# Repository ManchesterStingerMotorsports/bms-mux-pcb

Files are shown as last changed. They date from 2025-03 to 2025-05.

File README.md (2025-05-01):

# BMS MUX PCB

Initially the pcb scope was only for multiplexing 16 temperature sensor signals to 8, but the scope grew bigger and other stuffs were added.

Designed in Kicad V8

## V1 3D Render
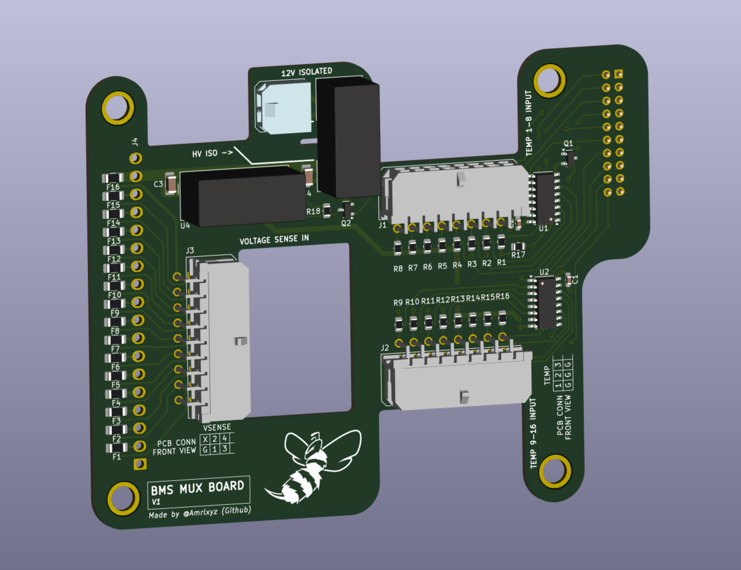
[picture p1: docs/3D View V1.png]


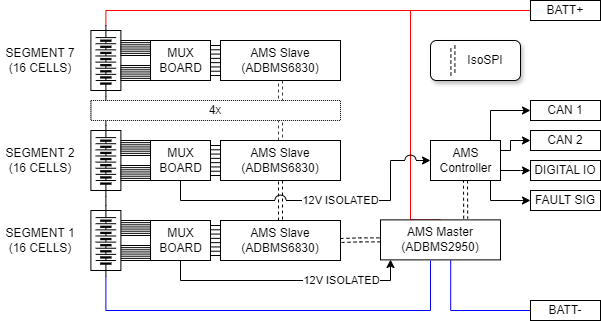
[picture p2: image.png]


### [Schematic](<docs/Schematic V1.pdf>)

### [Layout](<docs/PCB Layout V1.pdf>)

### [Copper Layers](<docs/PCB Copper Layers V1.pdf>)

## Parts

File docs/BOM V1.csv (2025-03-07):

Reference | Value | Datasheet | Footprint | Qty | DNP | Manufacturer Part Number
C1,C2 | 100n | ~ | Capacitor_SMD:C_0603_1608Metric_Pad1.08x0.95mm_HandSolder | 2 |  | CL10B104KB85PND
C3,C4 | 2.2u | ~ | Capacitor_SMD:C_1206_3216Metric_Pad1.33x1.80mm_HandSolder | 2 |  | 885382208016
F1,F2,F3,F4,F5,F6,F7,F8,F9,F10,F11,F12,F13,F14,F15,F16 | Fuse | ~ | Fuse:Fuse_1206_3216Metric_Pad1.42x1.75mm_HandSolder | 16 |  | 0466.250NR
J1,J2 | Conn_02x08_Counter_Clockwise | ~ | BMS-Mux-footprints:Molex_Micro-Fit_3.0_43045-1600_2x08_P3.00mm_Horizontal | 2 |  | 43045-1600
J3 | Conn_02x09_Top_Bottom | ~ | BMS-Mux-footprints:Molex_Micro-Fit_3.0_43045-1800_2x09_P3.00mm_Horizontal | 1 |  | 43045-1800
J4 | Conn_01x18 | ~ | Connector_Wago:Wago_734-148_1x18_P3.50mm_Vertical | 1 |  | 1945151 (x2)
J5 | Conn_01x02 | ~ | BMS-Mux-footprints:Molex_Micro-Fit_3.0_43650-0200_1x02_P3.00mm_Horizontal | 1 |  | 43650-0200
J6 | Conn_02x10_Odd_Even | ~ | Connector_PinHeader_2.54mm:PinHeader_2x10_P2.54mm_Vertical | 1 |  | PH2-20-UA
Q1,Q2 | BSS123 | http://www.diodes.com/assets/Datasheets/ds30366.pdf | Package_TO_SOT_SMD:SOT-23 | 2 |  | BSS123L
R1,R2,R3,R4,R5,R6,R7,R8,R9,R10,R11,R12,R13,R14,R15,R16 | 680R | ~ | Resistor_SMD:R_0805_2012Metric | 16 |  | ERA-6AEB681V
R17,R18 | 16k | ~ | Resistor_SMD:R_0805_2012Metric | 2 |  | ERA-6AEB163V
U1,U2 | 74CBTLV3257 | http://www.ti.com/lit/ds/symlink/sn74cbtlv3257.pdf | Package_SO:SOIC-16_3.9x9.9mm_P1.27mm | 2 |  | SN74LV4053ADR
U3 | TEC2-4812WI | https://www.tracopower.com/products/tec2wi.pdf | Converter_DCDC:Converter_DCDC_TRACO_TMR-xxxx_THT | 1 |  | TEC2-4812WI
U4 | TEC2-4810WI | https://www.tracopower.com/products/tec2wi.pdf | Converter_DCDC:Converter_DCDC_TRACO_TMR-xxxx_THT | 1 |  | TEC2-4810WI

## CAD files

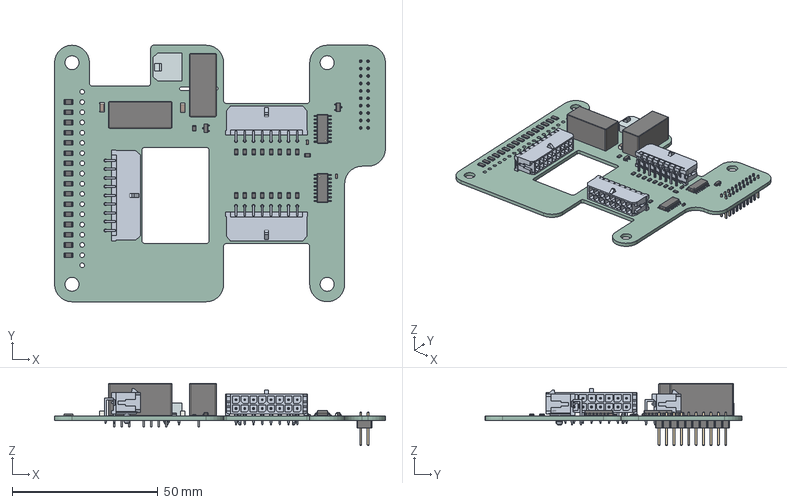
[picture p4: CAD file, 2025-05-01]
docs/BMS-Mux-PCB.step
113.5 x 88.0 x 21.3 mm
R_0805_2012Metric x 18
C_1206_3216Metric x 2
Fuse_1206_3216Metric x 16
436500200wbm000_01
Converter_DCDC_TRACO_TMR_xxxx_THT x 2
SOT_23 x 2
SOIC_16_39x99mm_P127mm x 2
C_0603_1608Metric x 2
PinHeader_2x10_P254mm_Vertical
BMS-Mux-PCB_PCB

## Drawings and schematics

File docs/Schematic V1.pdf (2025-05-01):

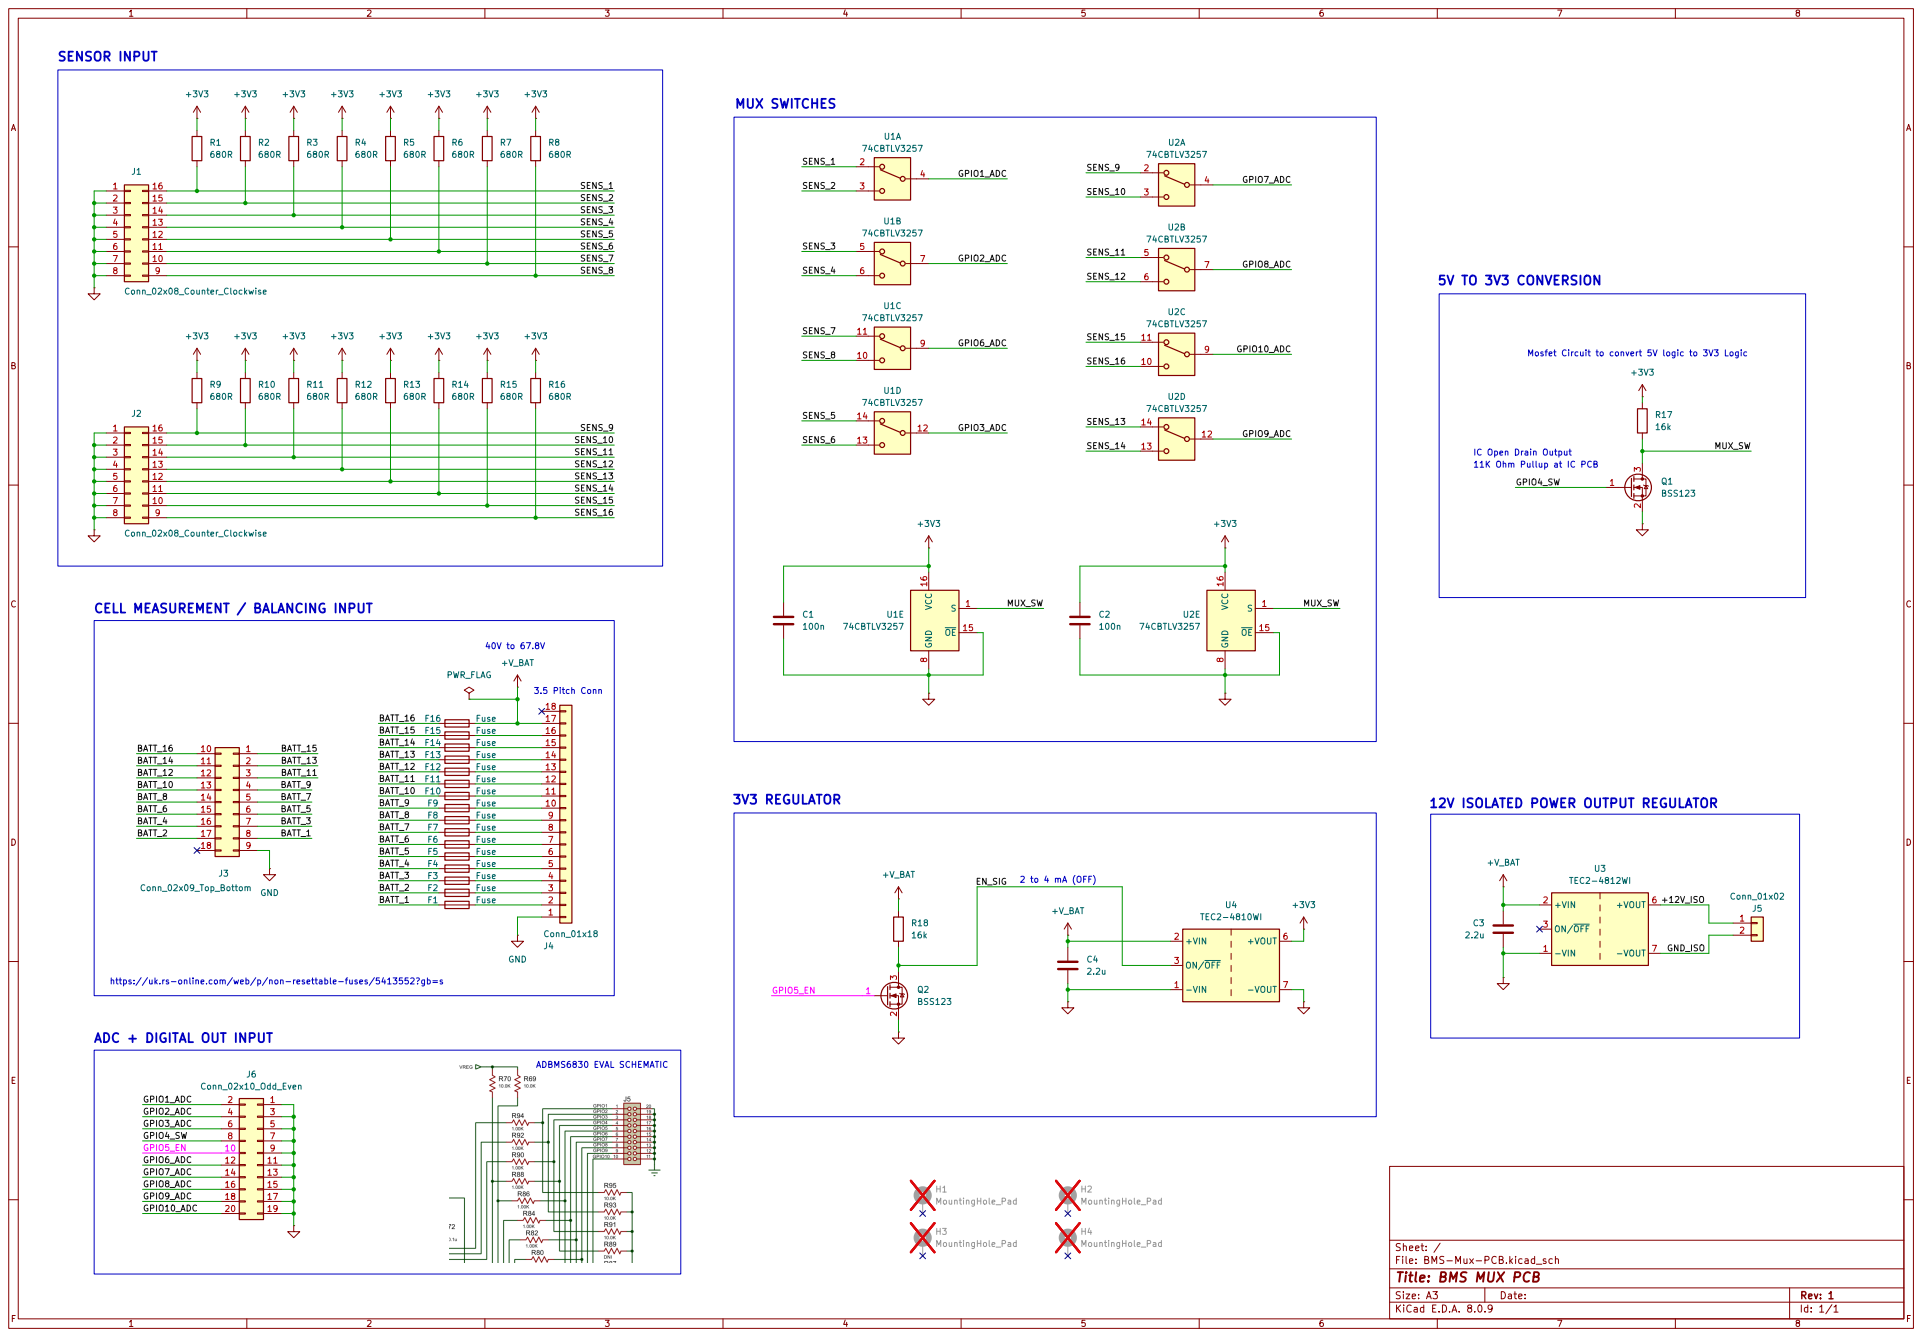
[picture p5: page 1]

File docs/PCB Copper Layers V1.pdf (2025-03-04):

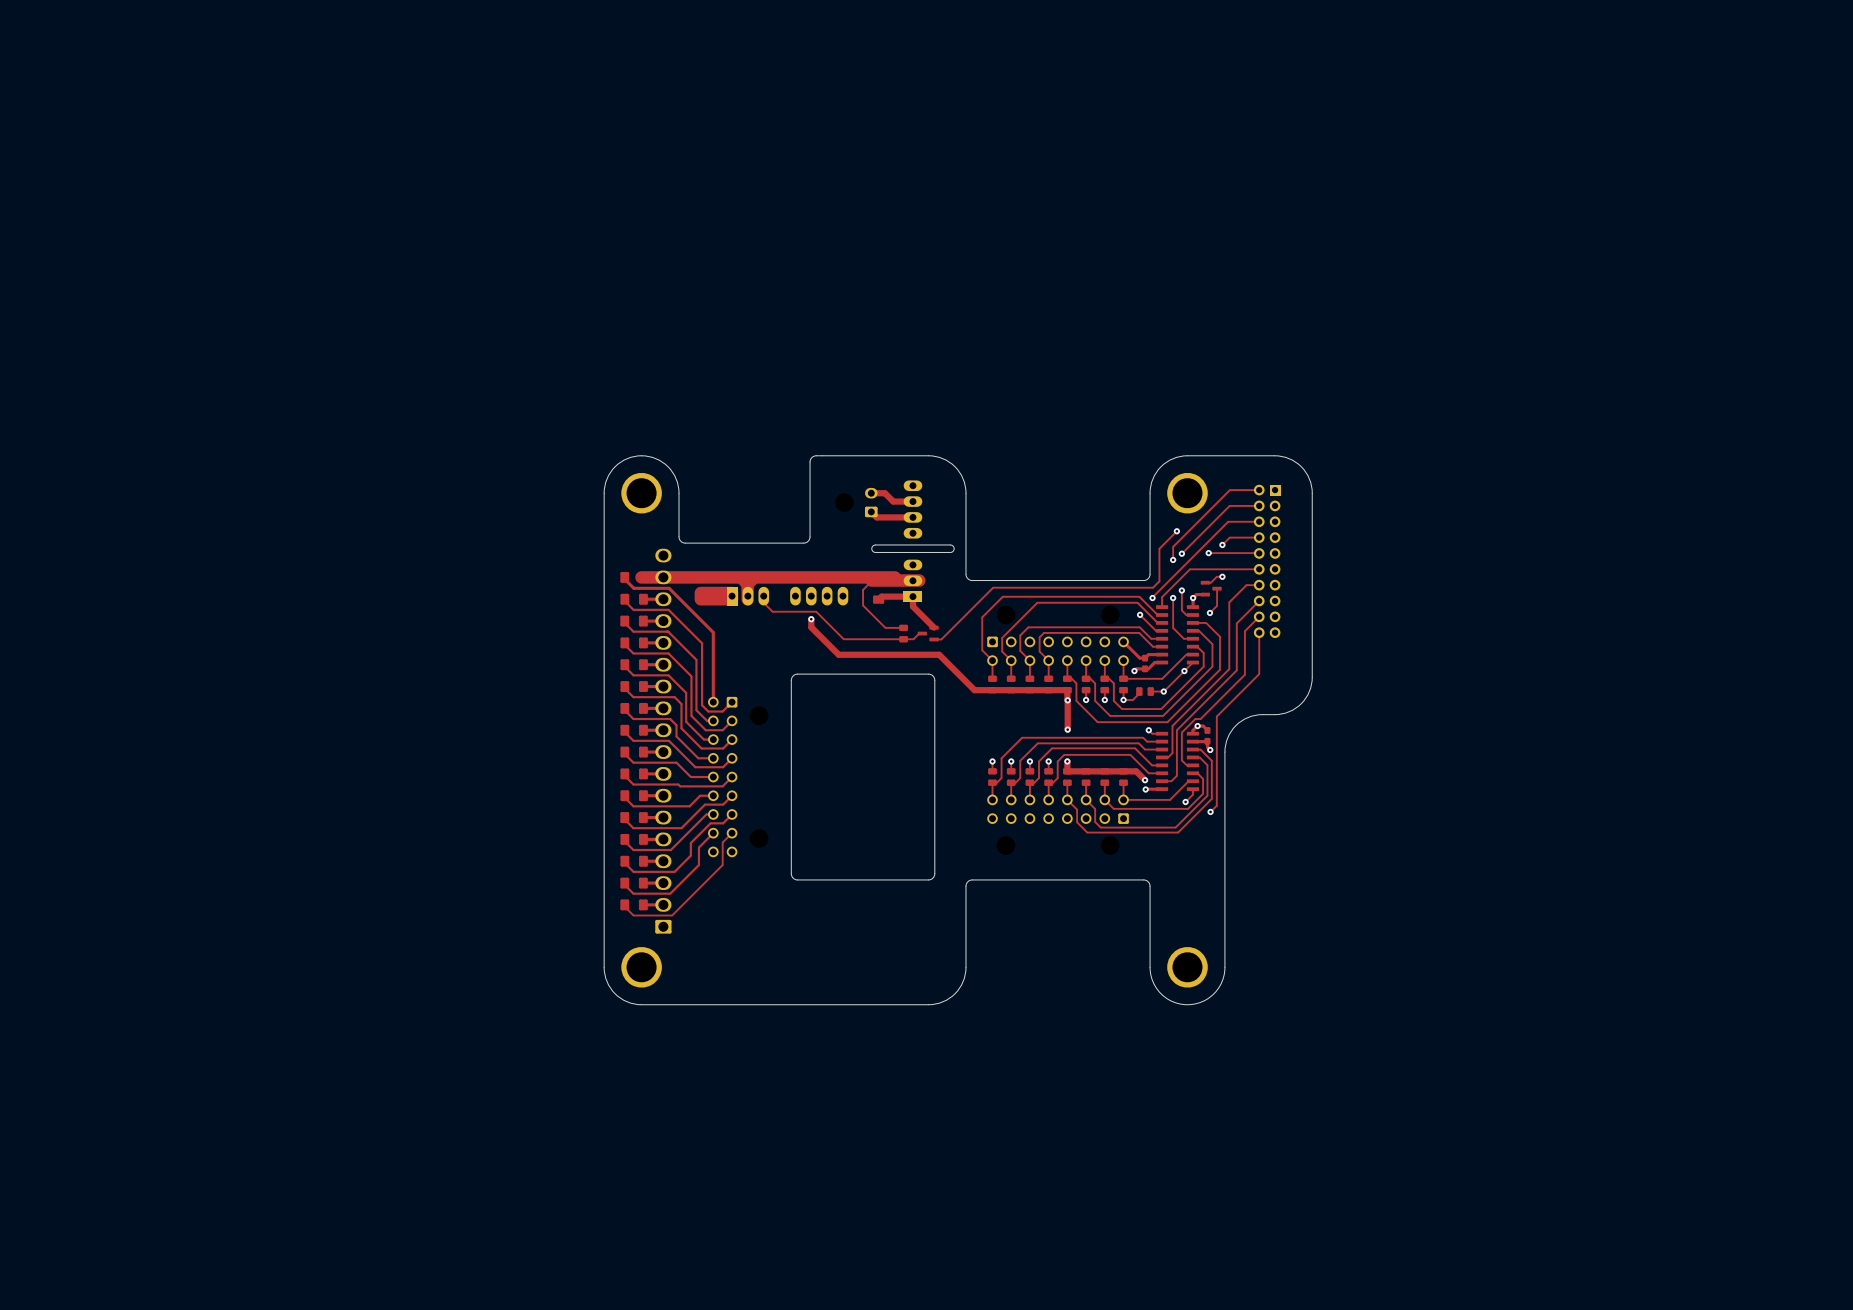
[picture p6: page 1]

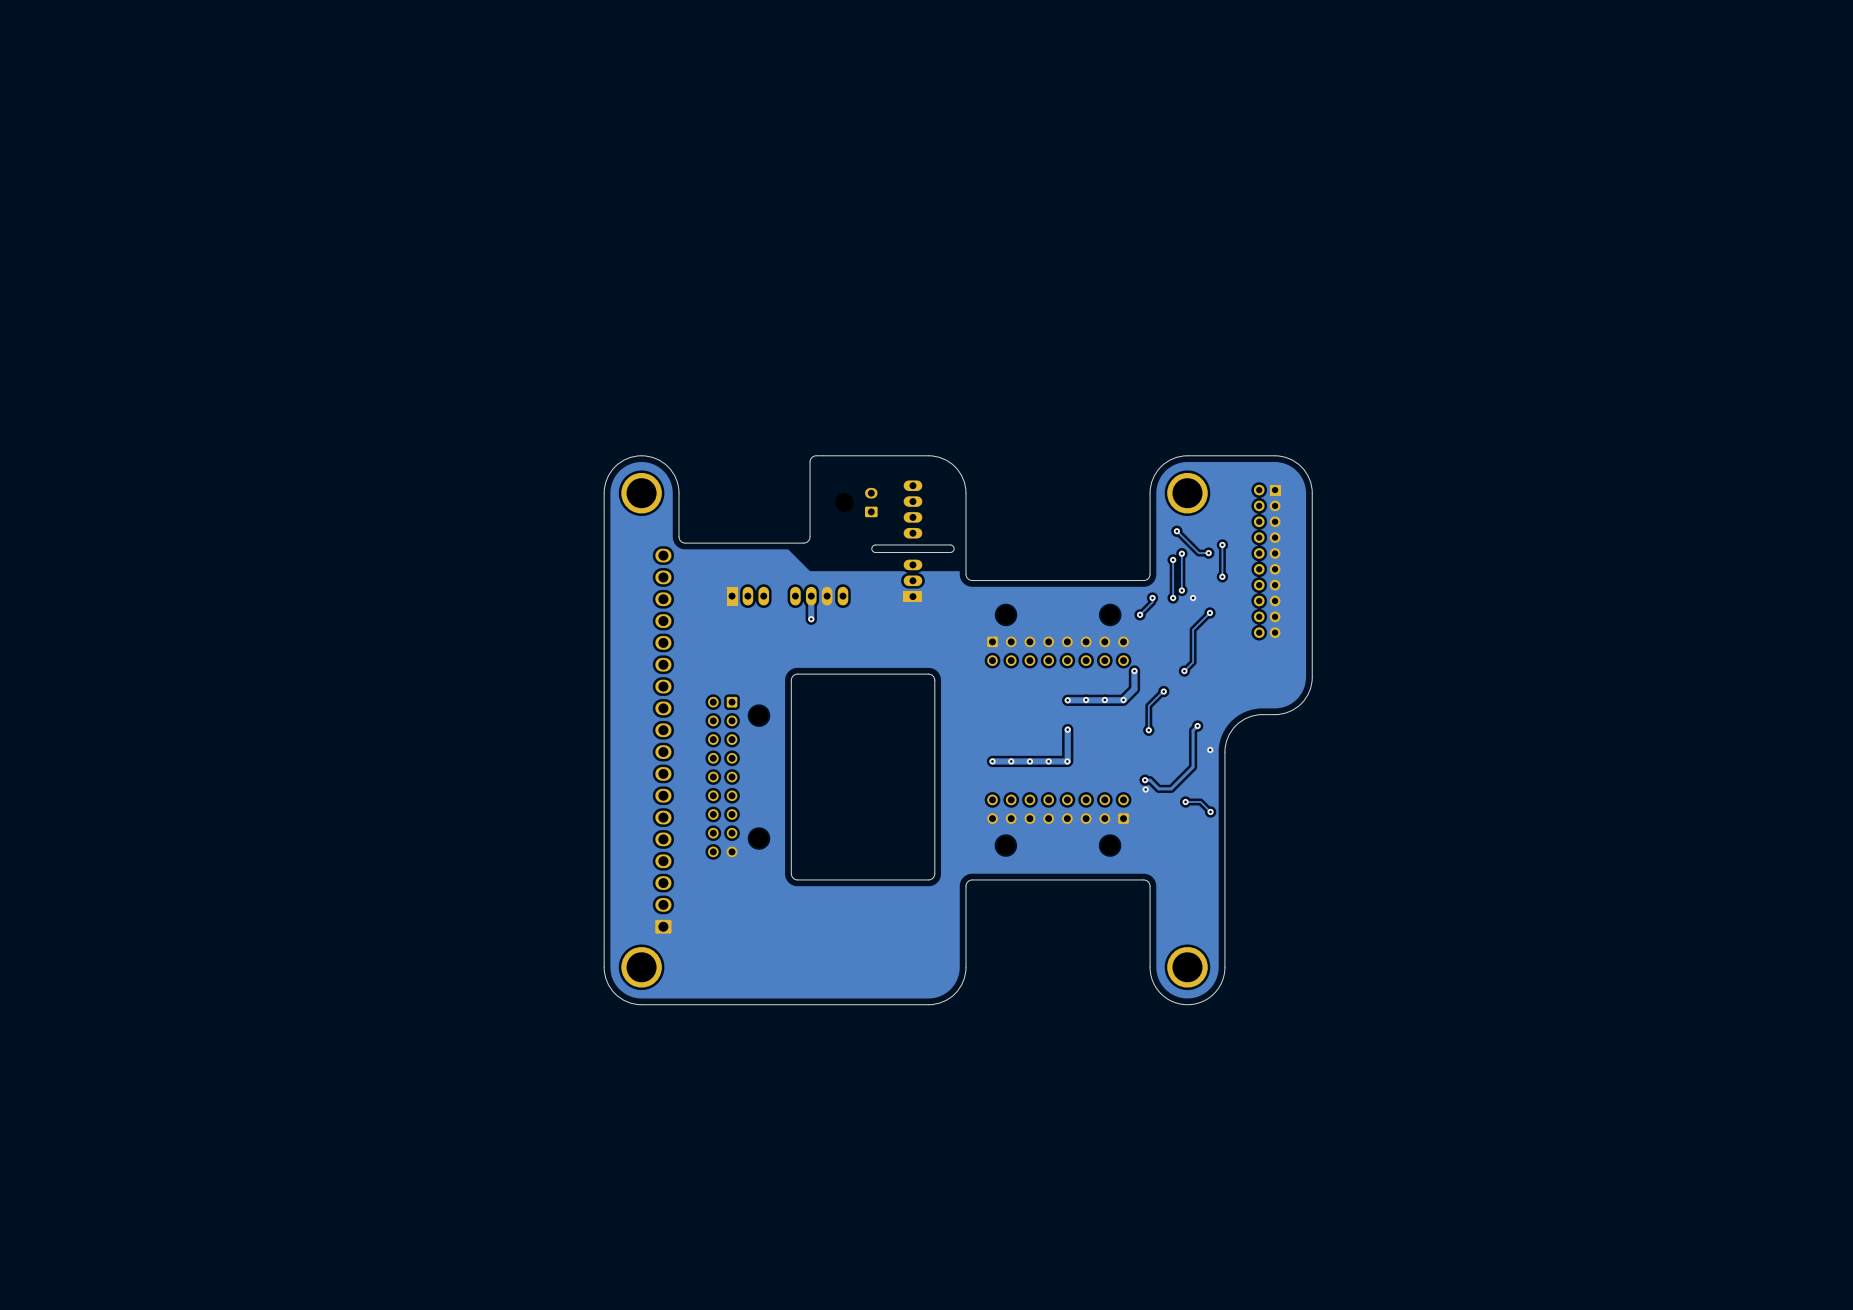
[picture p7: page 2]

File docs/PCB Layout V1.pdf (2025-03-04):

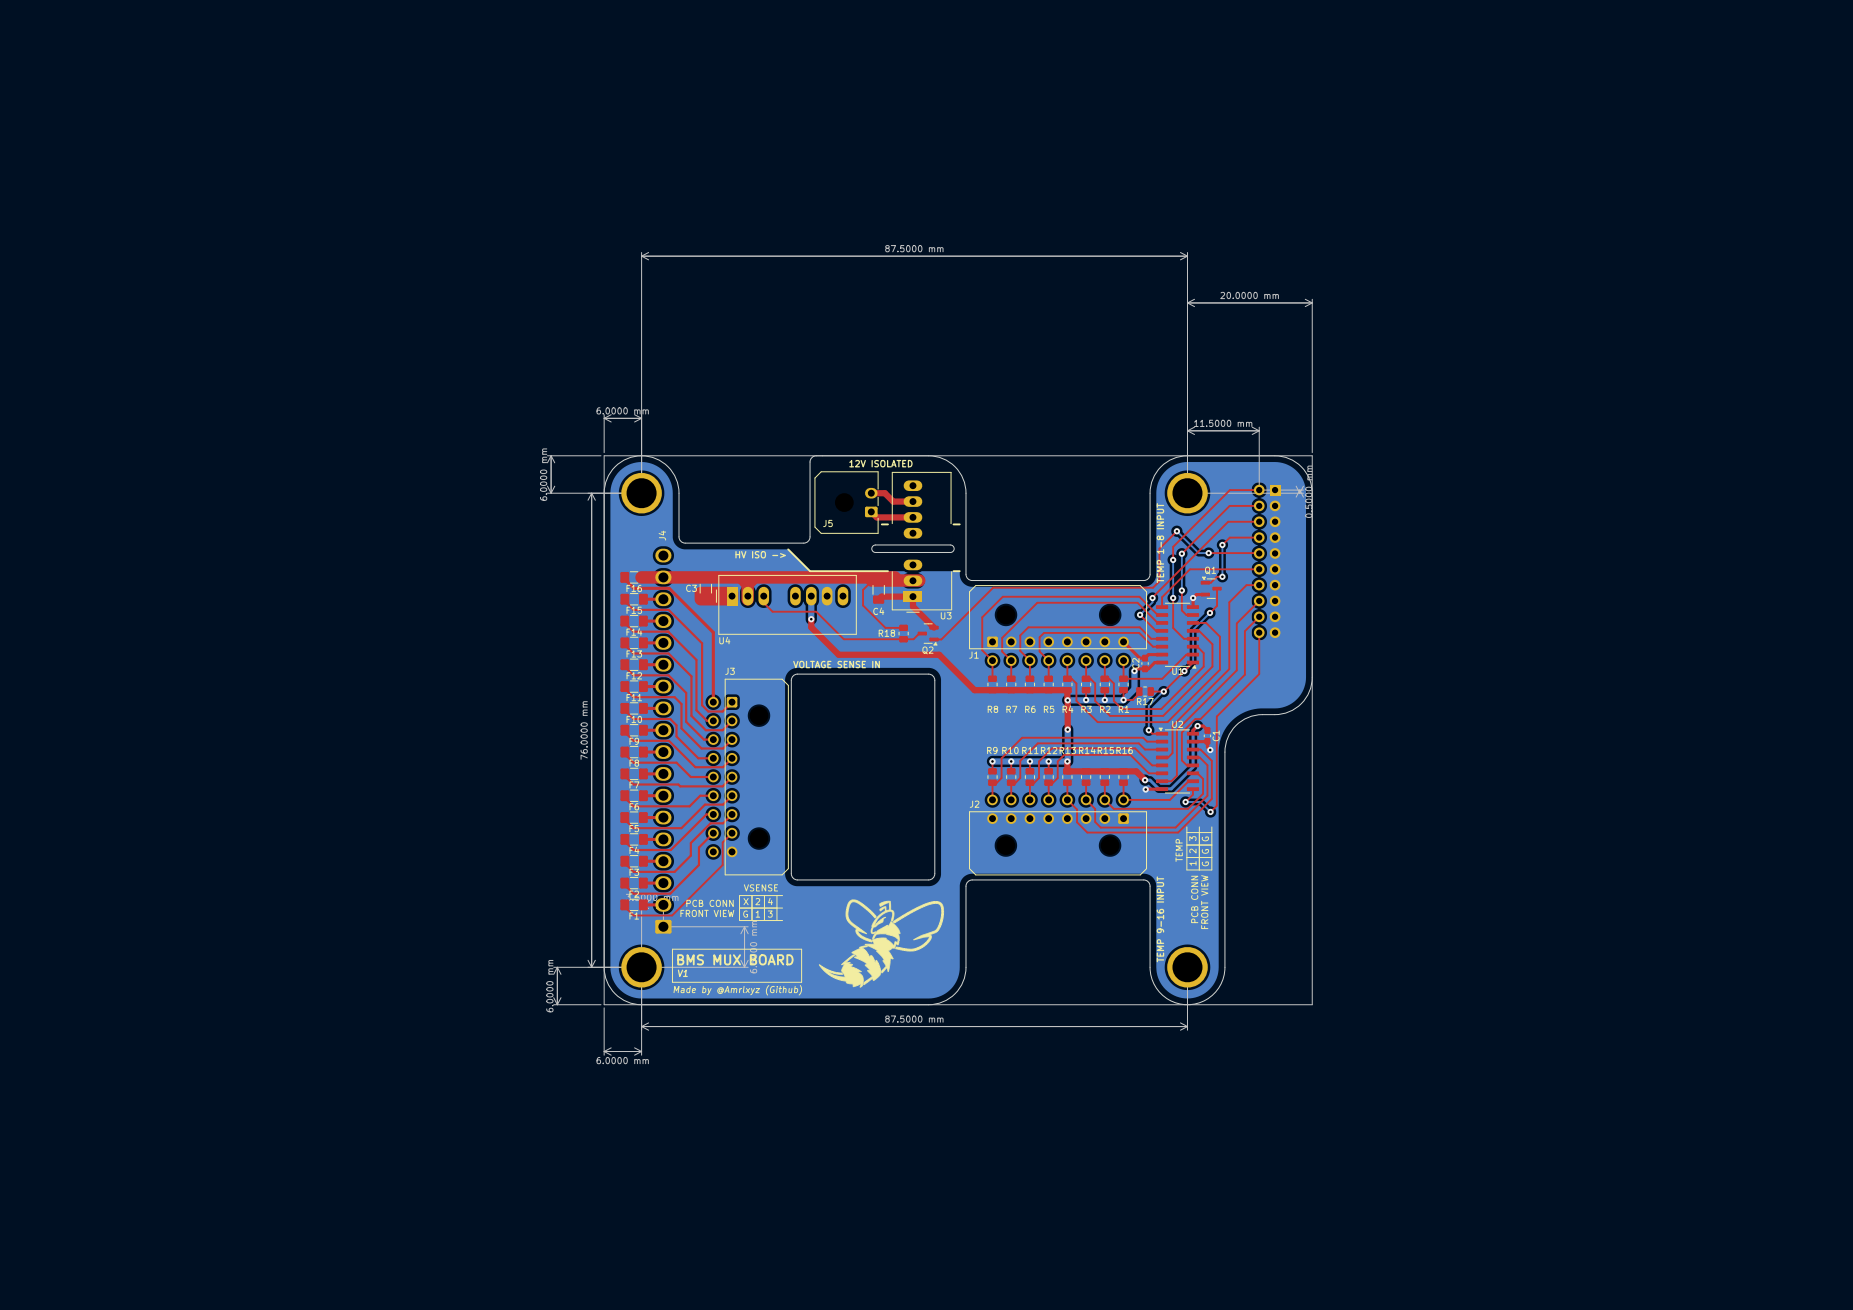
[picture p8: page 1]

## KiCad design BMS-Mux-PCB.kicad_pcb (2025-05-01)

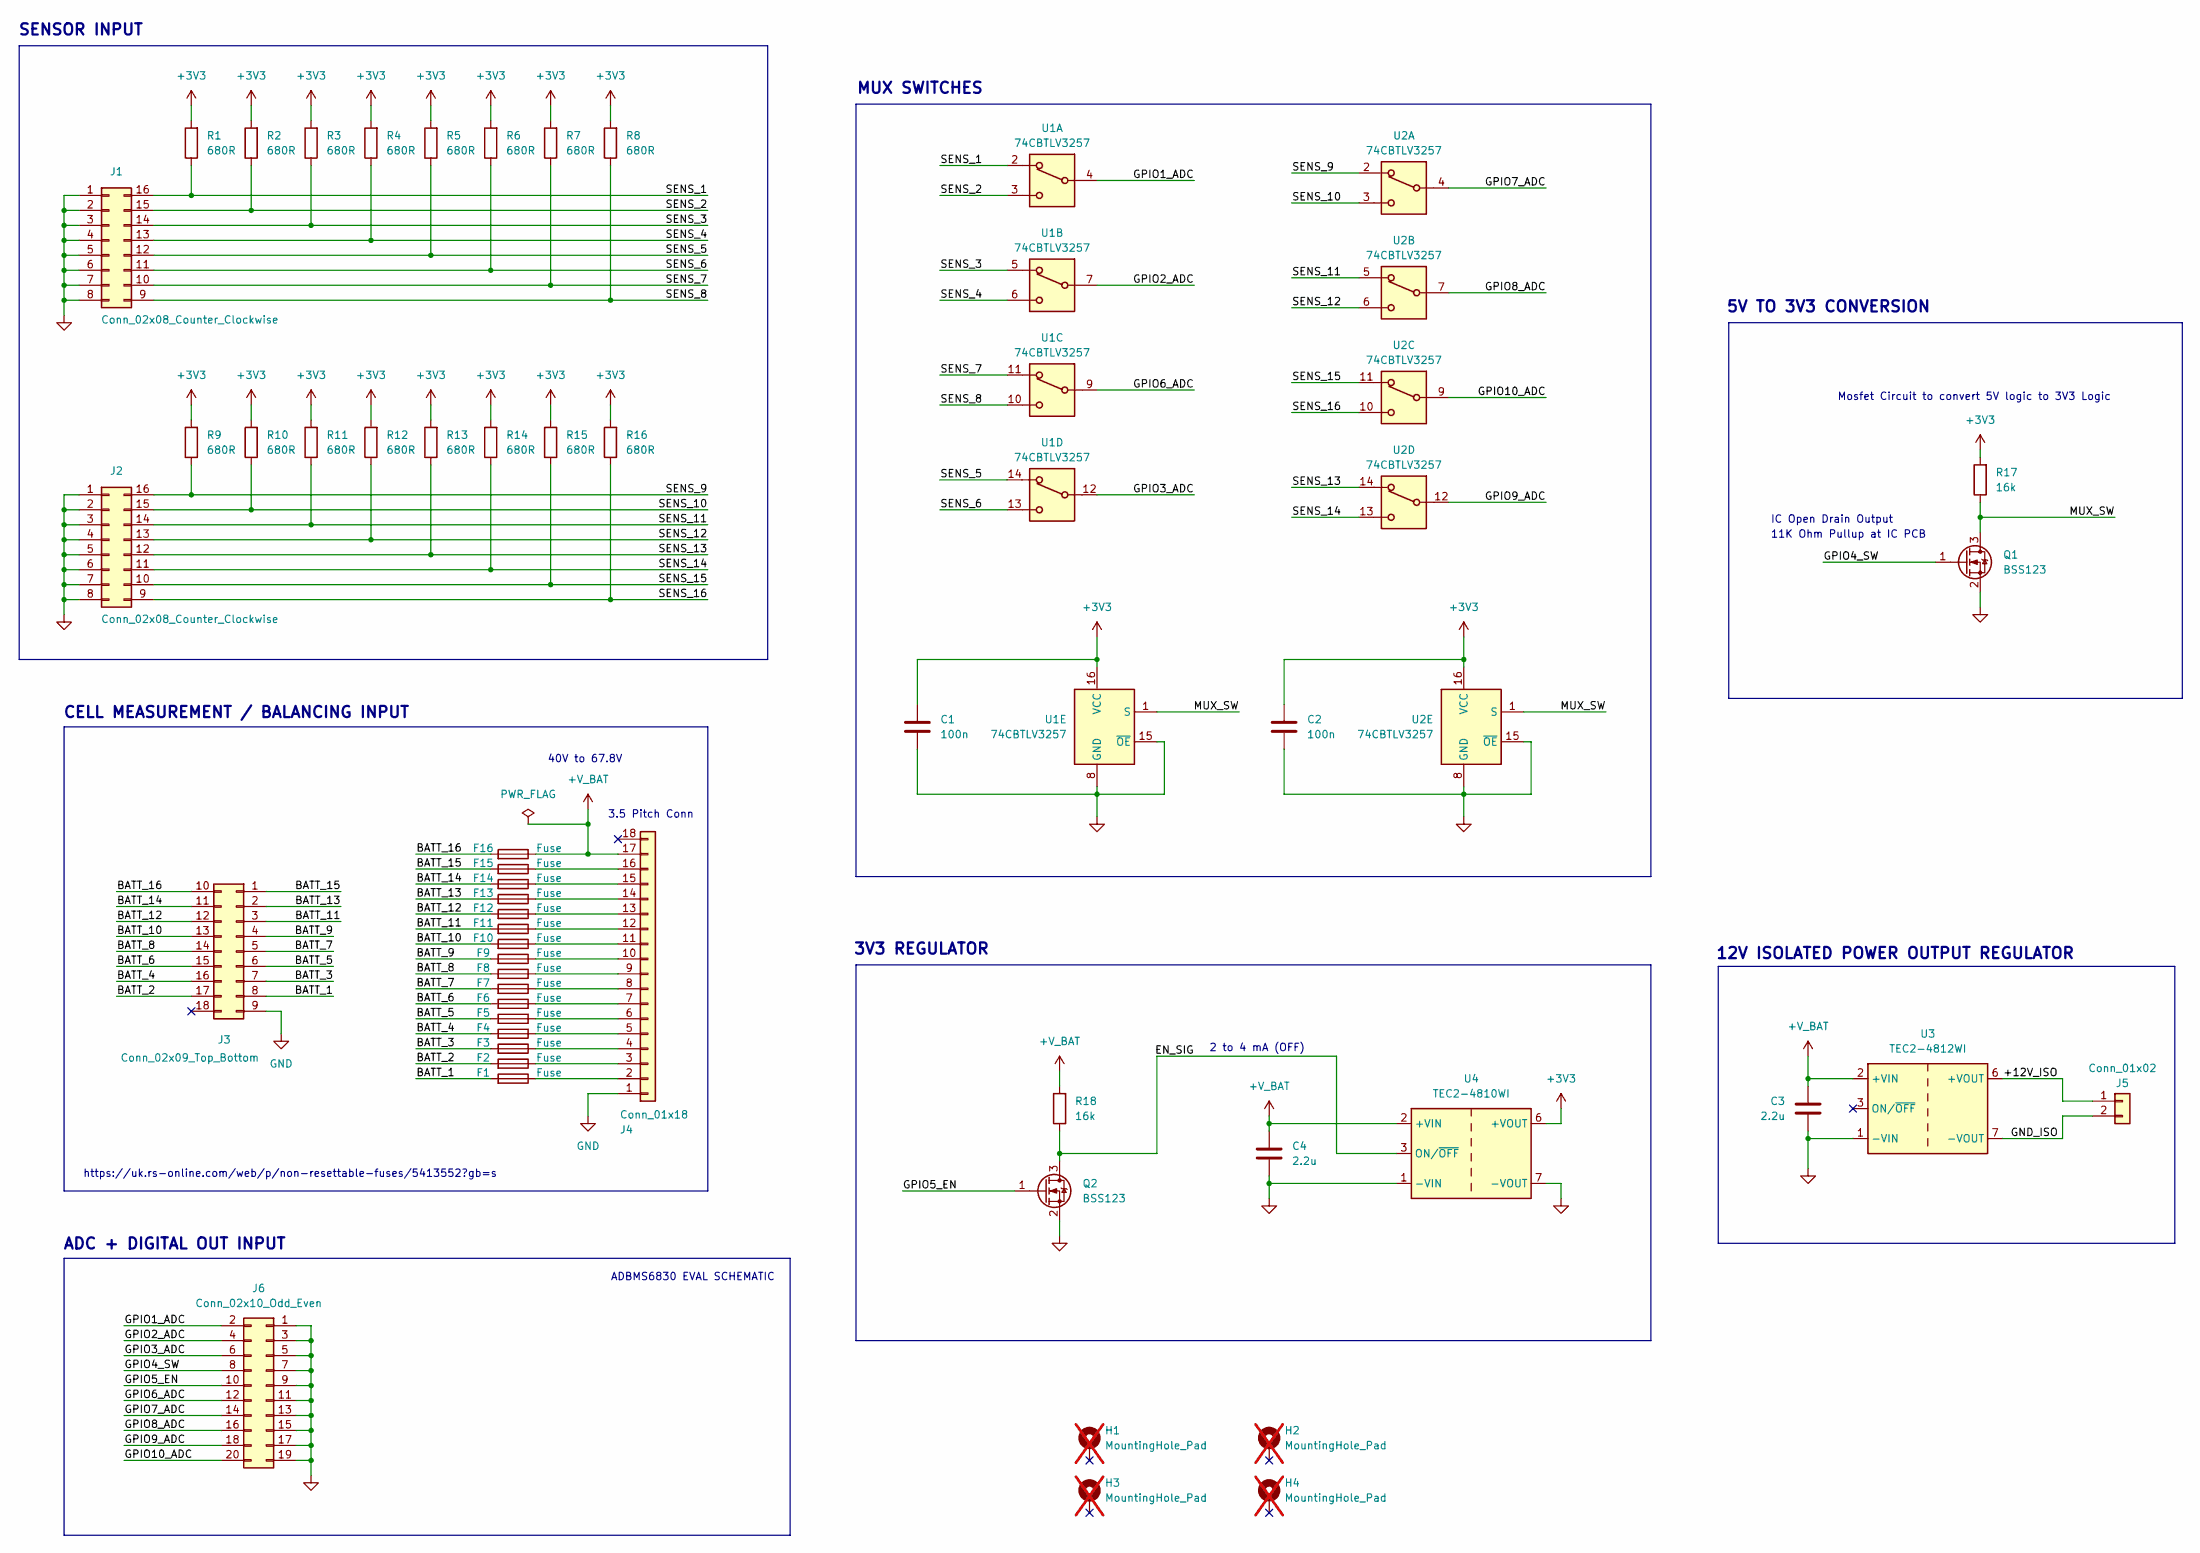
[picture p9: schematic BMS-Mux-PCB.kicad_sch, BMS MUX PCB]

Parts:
C1, C2: 100n; C_0603_1608Metric_Pad1.08x0.95mm_HandSolder; Manufacturer Part Number CL10B104KB85PND
C3, C4: 2.2u; C_1206_3216Metric_Pad1.33x1.80mm_HandSolder; Manufacturer Part Number 885382208016
F1, F2, F3, F4, F5, F6, F7, F8, F9, F10, F11, F12, F13, F14, F15, F16: Fuse; Fuse_1206_3216Metric_Pad1.42x1.75mm_HandSolder; Manufacturer Part Number 0466.250NR
H1, H2, H3, H4: MountingHole_Pad; Mounting_Hole; not fitted
J1, J2: Conn_02x08_Counter_Clockwise; Molex_Micro-Fit_3.0_43045-1600_2x08_P3.00mm_Horizontal; Manufacturer Part Number 43045-1600
J3: Conn_02x09_Top_Bottom; Molex_Micro-Fit_3.0_43045-1800_2x09_P3.00mm_Horizontal; Manufacturer Part Number 43045-1800
J4: Conn_01x18; Wago_734-148_1x18_P3.50mm_Vertical; Manufacturer Part Number 1945151 (x2)
J5: Conn_01x02; Molex_Micro-Fit_3.0_43650-0200_1x02_P3.00mm_Horizontal; Manufacturer Part Number 43650-0200
J6: Conn_02x10_Odd_Even; PinHeader_2x10_P2.54mm_Vertical; Manufacturer Part Number PH2-20-UA
Q1, Q2: BSS123; SOT-23; Manufacturer Part Number BSS123L
R1, R2, R3, R4, R5, R6, R7, R8, R9, R10, R11, R12, R13, R14, R15, R16: 680R; R_0805_2012Metric; Manufacturer Part Number ERA-6AEB681V
R17, R18: 16k; R_0805_2012Metric; Manufacturer Part Number ERA-6AEB163V
U1, U2: 74CBTLV3257; SOIC-16_3.9x9.9mm_P1.27mm; Manufacturer Part Number SN74LV4053ADR
U3: TEC2-4812WI; Converter_DCDC_TRACO_TMR-xxxx_THT; Manufacturer Part Number TEC2-4812WI
U4: TEC2-4810WI; Converter_DCDC_TRACO_TMR-xxxx_THT; Manufacturer Part Number TEC2-4810WI

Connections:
+3V3: C1.1, C2.1, R1.2, R2.2, R3.2, R4.2, R5.2, R6.2, R7.2, R8.2, R9.2, R10.2, R11.2, R12.2, R13.2, R14.2, R15.2, R16.2, R17.2, U1.16 (VCC), U2.16 (VCC), U4.6 (+VOUT)
+V_BAT: C3.1, C4.1, F16.1, J4.17, R18.2, U3.2 (+VIN), U4.2 (+VIN)
/+12V_ISO: J5.1, U3.6 (+VOUT)
/BATT_1: F1.2, J3.8
/BATT_2: F2.2, J3.17
/BATT_3: F3.2, J3.7
/BATT_4: F4.2, J3.16
/BATT_5: F5.2, J3.6
/BATT_6: F6.2, J3.15
/BATT_7: F7.2, J3.5
/BATT_8: F8.2, J3.14
/BATT_9: F9.2, J3.4
/BATT_10: F10.2, J3.13
/BATT_11: F11.2, J3.3
/BATT_12: F12.2, J3.12
/BATT_13: F13.2, J3.2
/BATT_14: F14.2, J3.11
/BATT_15: F15.2, J3.1
/BATT_16: F16.2, J3.10
/EN_SIG: Q2.3 (D), R18.1, U4.3 (ON/~OFF)
/GND_ISO: J5.2, U3.7 (-VOUT)
/GPIO1_ADC: J6.2, U1.4
/GPIO2_ADC: J6.4, U1.7
/GPIO3_ADC: J6.6, U1.12
/GPIO4_SW: J6.8, Q1.1 (G)
/GPIO5_EN: J6.10, Q2.1 (G)
/GPIO6_ADC: J6.12, U1.9
/GPIO7_ADC: J6.14, U2.4
/GPIO8_ADC: J6.16, U2.7
/GPIO9_ADC: J6.18, U2.12
/GPIO10_ADC: J6.20, U2.9
/MUX_SW: Q1.3 (D), R17.1, U1.1 (S), U2.1 (S)
/SENS_1: J1.16, R1.1, U1.2
/SENS_2: J1.15, R2.1, U1.3
/SENS_3: J1.14, R3.1, U1.5
/SENS_4: J1.13, R4.1, U1.6
/SENS_5: J1.12, R5.1, U1.14
/SENS_6: J1.11, R6.1, U1.13
/SENS_7: J1.10, R7.1, U1.11
/SENS_8: J1.9, R8.1, U1.10
/SENS_9: J2.16, R9.1, U2.2
/SENS_10: J2.15, R10.1, U2.3
/SENS_11: J2.14, R11.1, U2.5
/SENS_12: J2.13, R12.1, U2.6
/SENS_13: J2.12, R13.1, U2.14
/SENS_14: J2.11, R14.1, U2.13
/SENS_15: J2.10, R15.1, U2.11
/SENS_16: J2.9, R16.1, U2.10
GND: C1.2, C2.2, C3.2, C4.2, J1.1, J1.2, J1.3, J1.4, J1.5, J1.6, J1.7, J1.8, J2.1, J2.2, J2.3, J2.4, J2.5, J2.6, J2.7, J2.8, J3.9, J4.1, J6.1, J6.3, J6.5, J6.7, J6.9, J6.11, J6.13, J6.15, J6.17, J6.19, Q1.2 (S), Q2.2 (S), U1.8 (GND), U1.15 (~OE), U2.8 (GND), U2.15 (~OE), U3.1 (-VIN), U4.1 (-VIN), U4.7 (-VOUT)
unnamed: F1.1, J4.2
unnamed: F2.1, J4.3
unnamed: F3.1, J4.4
unnamed: F4.1, J4.5
unnamed: F5.1, J4.6
unnamed: F6.1, J4.7
unnamed: F7.1, J4.8
unnamed: F8.1, J4.9
unnamed: F9.1, J4.10
unnamed: F10.1, J4.11
unnamed: F11.1, J4.12
unnamed: F12.1, J4.13
unnamed: F13.1, J4.14
unnamed: F14.1, J4.15
unnamed: F15.1, J4.16

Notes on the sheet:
11K Ohm Pullup at IC PCB
SENSOR INPUT
ADBMS6830 EVAL SCHEMATIC
3V3 REGULATOR
40V to 67.8V
12V ISOLATED POWER OUTPUT REGULATOR
3.5 Pitch Conn
IC Open Drain Output
ADC + DIGITAL OUT INPUT
2 to 4 mA (OFF)
Mosfet Circuit to convert 5V logic to 3V3 Logic
MUX SWITCHES
https://uk.rs-online.com/web/p/non-resettable-fuses/5413552?gb=s
CELL MEASUREMENT / BALANCING INPUT
5V TO 3V3 CONVERSION

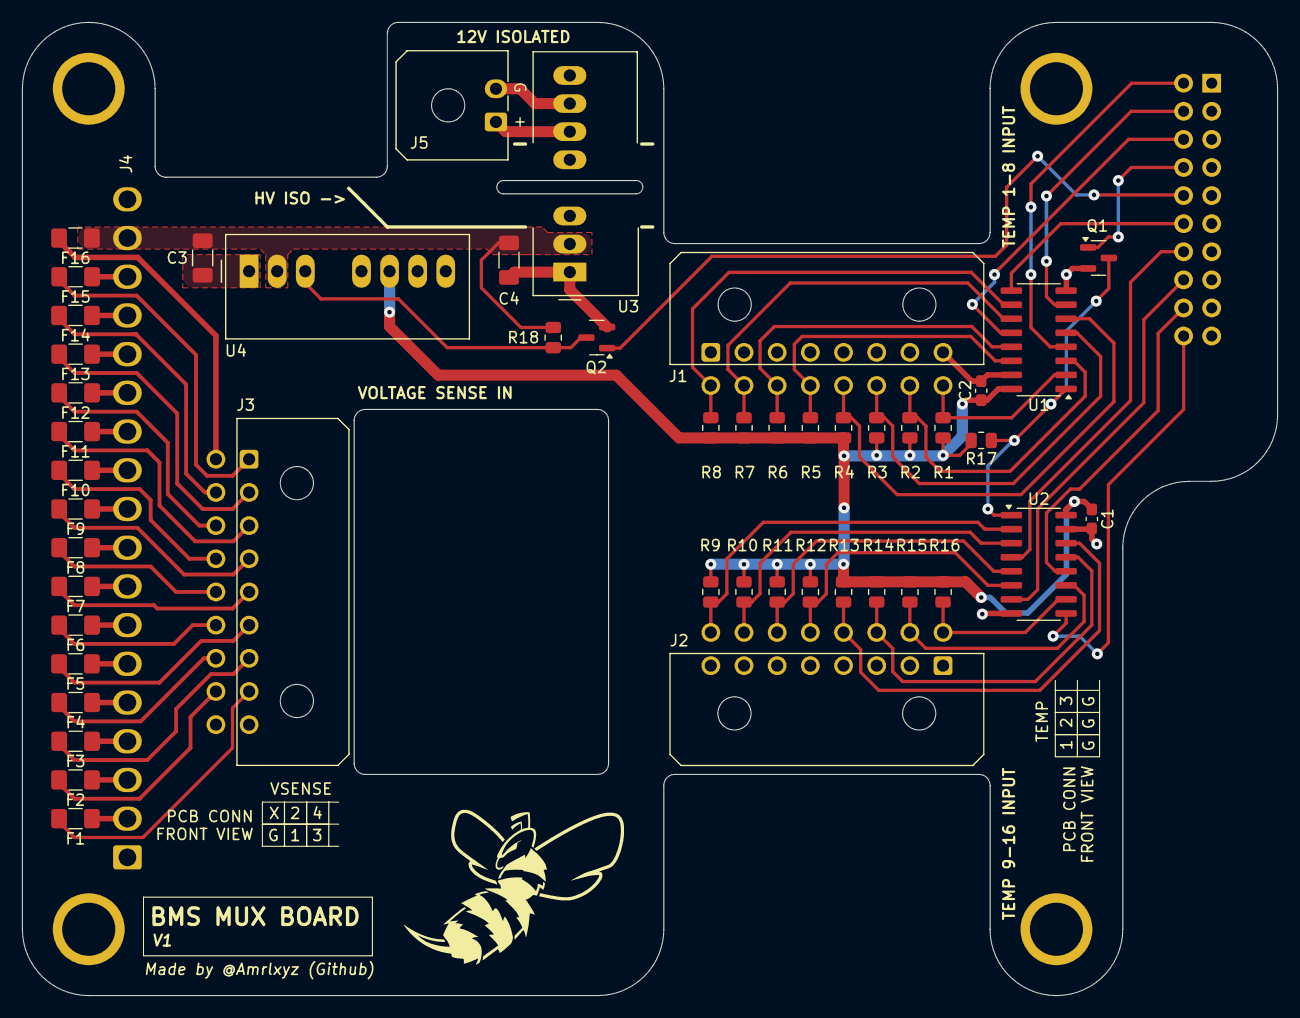
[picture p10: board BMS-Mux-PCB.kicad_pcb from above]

Board: 2 copper layers, 113.5 x 88.0 mm, 54 parts (1 on the bottom side), 64 nets.

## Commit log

2025-02-09 first commit - before removing mosfet circuit
    [BMS-Mux-PCB.kicad_pcb, BMS-Mux-PCB.kicad_sch]
2025-02-09 Finished Schematic -> fuse and connector footprint needs changing
    [BMS-Mux-PCB.kicad_pcb, BMS-Mux-PCB.kicad_sch]
2025-02-13 updated footprints and started layout
    [BMS-Mux-PCB.kicad_pcb, BMS-Mux-PCB.kicad_sch]
2025-02-14 added softreset command after reset
    [BMS-Mux-PCB.kicad_pcb, BMS-Mux-PCB.step]
2025-03-03 changed connector orientation and halfway routed
    [BMS-Mux-PCB.kicad_pcb, BMS-Mux-PCB.kicad_sch]
2025-03-04 V1 almost done - touching up silkscreen
    [BMS-Mux-PCB.kicad_pcb, BMS-Mux-PCB.kicad_sch]
2025-03-04 added pdfs and finalised V1
    [BMS-Mux-PCB.kicad_pcb]
2025-03-07 added some small changes for manufacturing purposes and gerber file generated
    [BMS-Mux-PCB-B_Cu.gbr, BMS-Mux-PCB-B_Mask.gbr, BMS-Mux-PCB-B_Paste.gbr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]
2025-05-01 fixed the gpio pin name number (minor fix)
    [BMS-Mux-PCB.kicad_pcb, BMS-Mux-PCB.kicad_sch, BMS-Mux-PCB.step]
2025-05-26 added gitignore
    [BMS-Mux-PCB.kicad_sch]
